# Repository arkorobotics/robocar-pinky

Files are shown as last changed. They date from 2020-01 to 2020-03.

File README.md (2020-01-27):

# Robocar - Pinky	

## Intro
Pinky is a 1/16 scale DIY autonomous car designed to compete in the [DIY Robocar](https://diyrobocars.com) race. Pinky also has a counterpart testbed named [Brain](Brain).

## Design

### Block Diagram
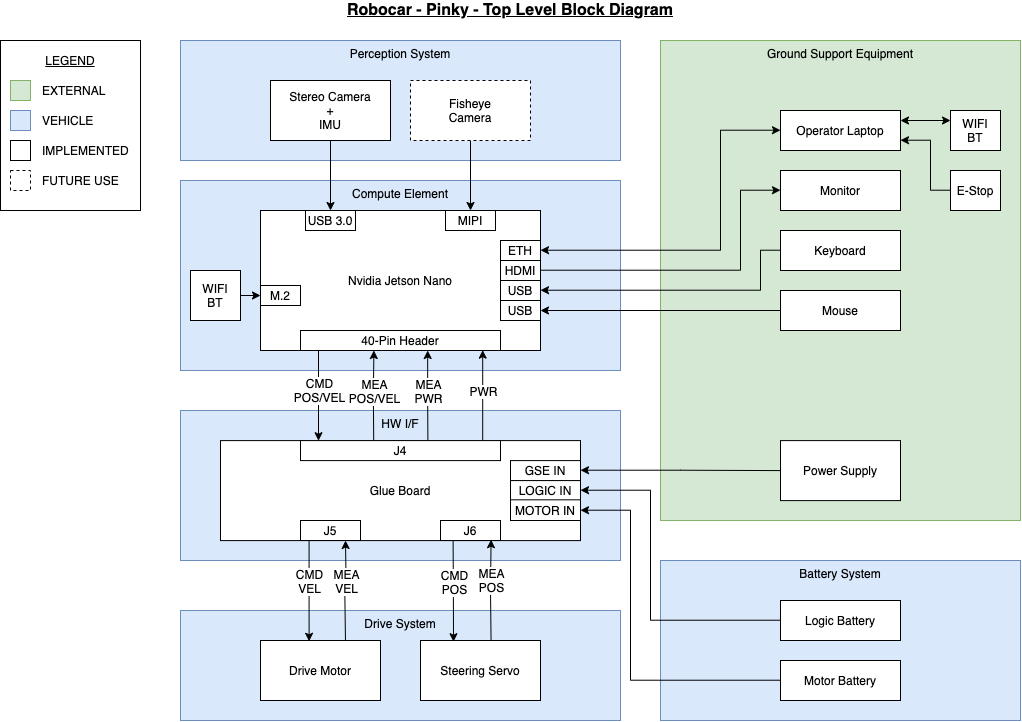
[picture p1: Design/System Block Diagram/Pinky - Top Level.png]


### Assembled Hardware
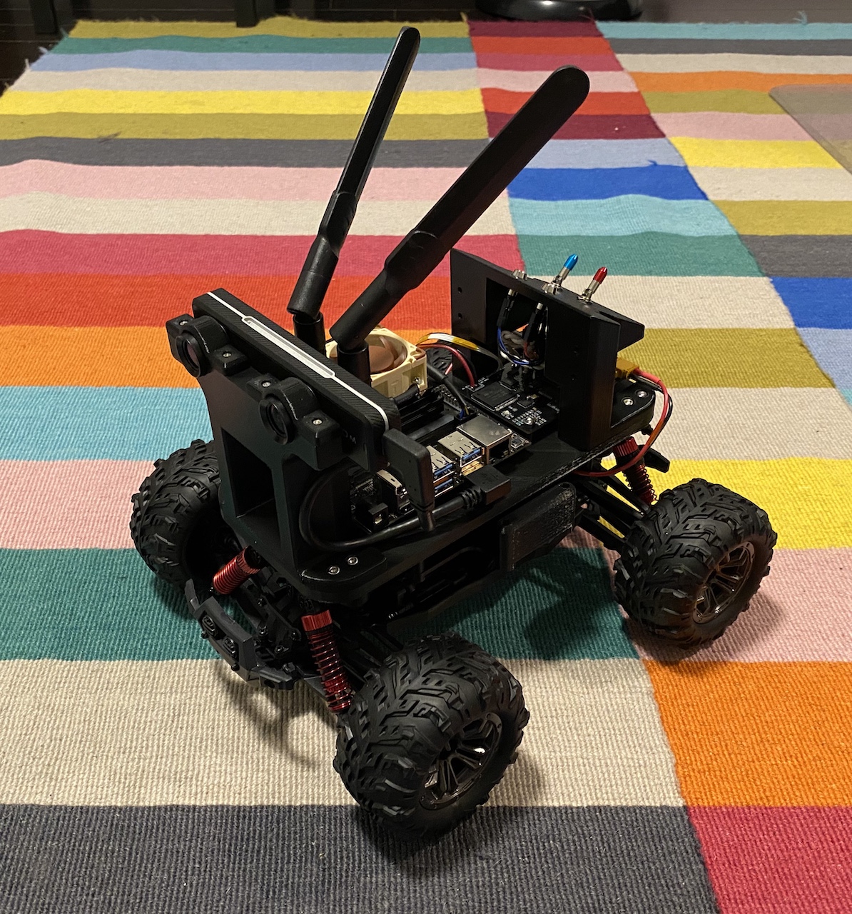
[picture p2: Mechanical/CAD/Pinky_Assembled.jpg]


## Software

See the [Software](./Software) subfolder.

## Hardware

### Perception System
Part | Cost  |  Link
------------ | ------------- | -------------
ZED Mini | $399.00 | [Stereo Labs Store](https://store.stereolabs.com/products/zed-mini)
IMX219 Camera Module (Fisheye) | $29.99  | [Amazon](https://www.amazon.com/gp/product/B07VFFRX4C)

### Compute Element
Part | Cost  |  Link
------------ | ------------- | -------------
NVIDIA Jetson Nano Developer Kit | $98.98 | [Amazon](https://www.amazon.com/gp/product/B07PZHBDKT/)
Intel Dual Band Wireless-Ac 8265 w/ BT Module | $21.55 | [Amazon](https://www.amazon.com/Intel-Dual-Band-Wireless-Ac-8265/dp/B01MZA1AB2)
Noctua Fan | $14.95 | [Amazon](https://www.amazon.com/gp/product/B071FNHVXN)

### Hardware Interface Board
Part | Cost  |  Link
------------ | ------------- | -------------
Glue Board (Fab/Assembly Required) | ~$300.00 | [GitHub](./Electronics/Glue%20Board)

### Drive System
Part | Cost  |  Link
------------ | ------------- | -------------
VATOS RC Car 9137R | $54.99 | [Amazon](https://www.amazon.com/gp/product/B07QRRJZDG/)

### Chassis
Part | Cost | Link
------------ | ------------- | -------------
Screw Set | $20.98 | [Amazon](https://www.amazon.com/gp/product/B07QLWPJKC/)
Threaded Heat Insert | $19.99 | [Amazon](https://www.amazon.com/gp/product/B07MWBJB67)
3D Printable Models (Fab/Assembly Required) | ~$20.00 | [GitHub](./Mechanical/CAD/STL%20Files)

### Other
Part | Cost  |  Link
------------ | ------------- | -------------
ENGPOW 7.4V 3000mah 30C Lipo Battery | $22.99 | [Amazon](https://www.amazon.com/gp/product/B075QDPSDQ/)
Samsung SD Car 128GB | $16.99 | [Amazon](https://www.amazon.com/gp/product/B06XWZWYVP/)
1.5 ft/50cm Micro USB 3.0 Cable | $8.79 | [Amazon](https://www.amazon.com/gp/product/B075CL915V/)
5V/4A 20W Switching Power | $8.99 | [Amazon](https://www.amazon.com/gp/product/B01N4HYWAM/)
WiFi/BT Antennas | $13.99 | [Amazon](https://www.amazon.com/gp/product/B01E29566W/)
USB 3.1 Right Angle A to Right Angle C | $19.25 | [UsbFirewire](https://www.usbfirewire.com/parts/rr-arch-xxg.html#RR-ARCH-10GRC)

### Harnessing
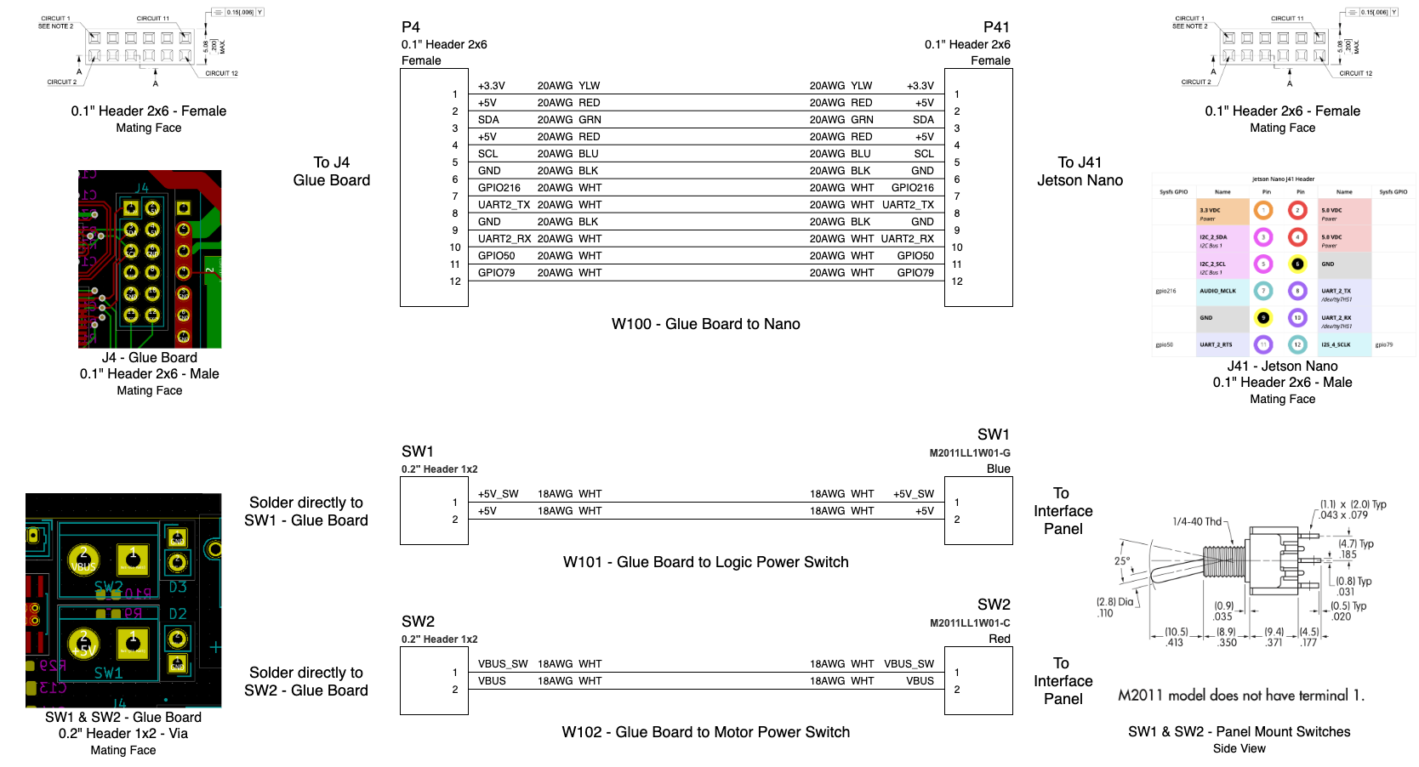
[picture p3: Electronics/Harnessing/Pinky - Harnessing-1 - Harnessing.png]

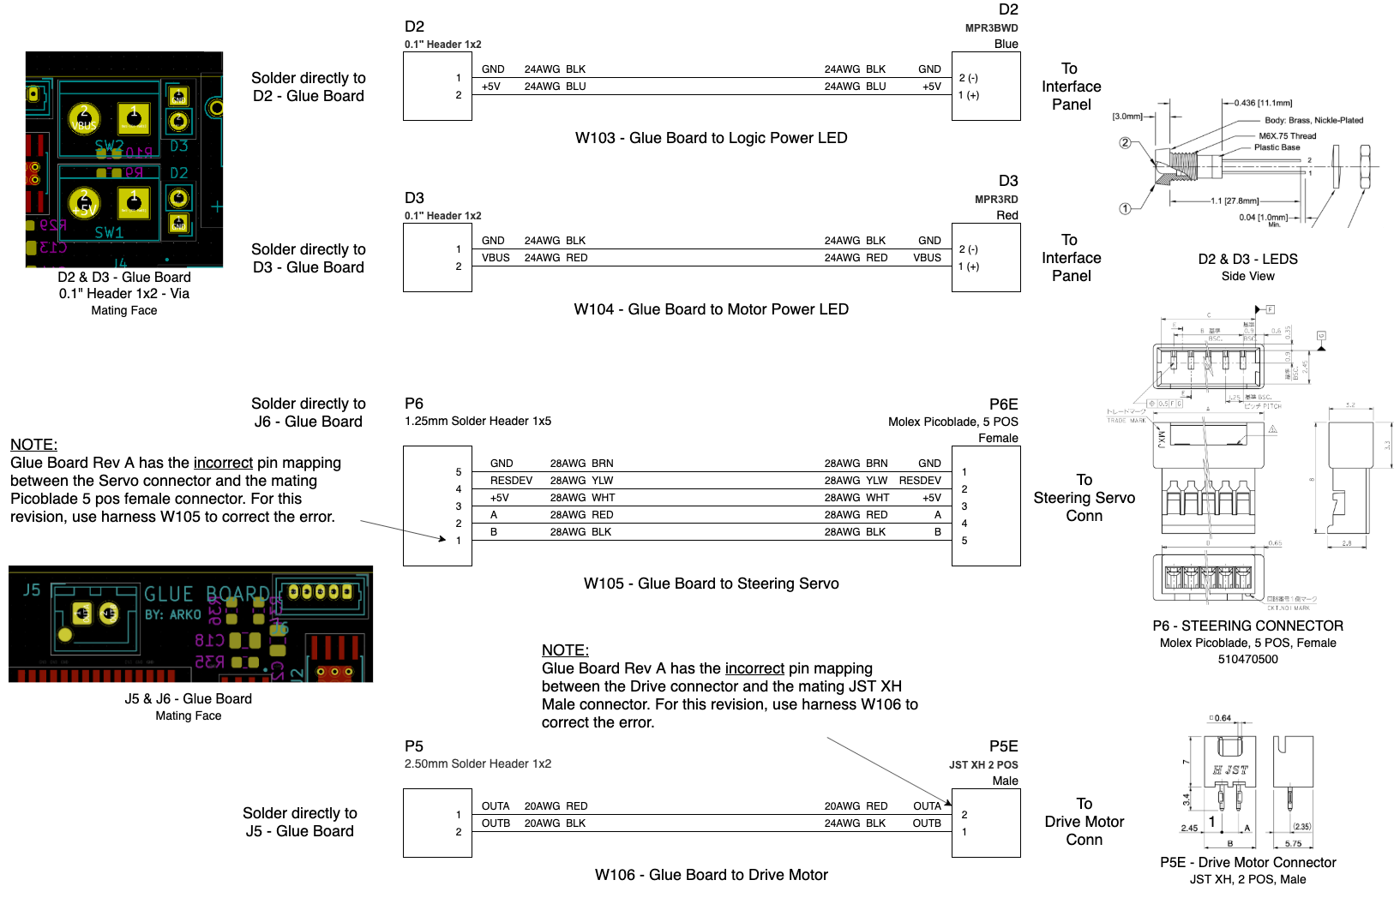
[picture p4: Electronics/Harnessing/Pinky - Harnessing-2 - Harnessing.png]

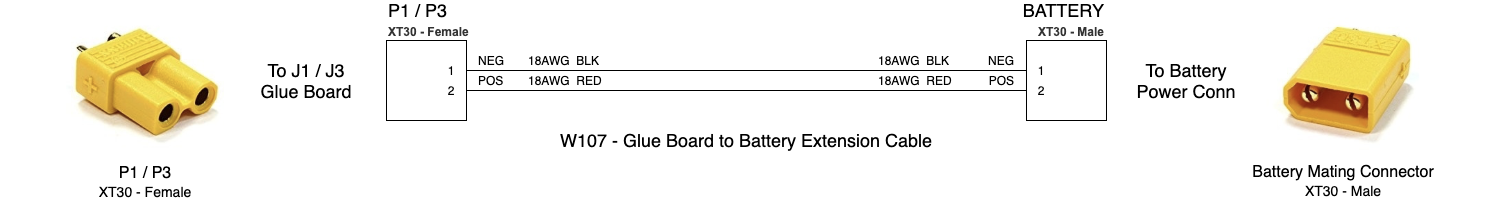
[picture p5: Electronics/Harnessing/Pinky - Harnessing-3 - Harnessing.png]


## Assembly

For 3D printed models, use the [Autodesk Fusion 360 Pinky CAD](./Mechanical/CAD/Pinky%20Assembly%20v27.f3z) model for assembly.

For electrical assembly, see diagram below:

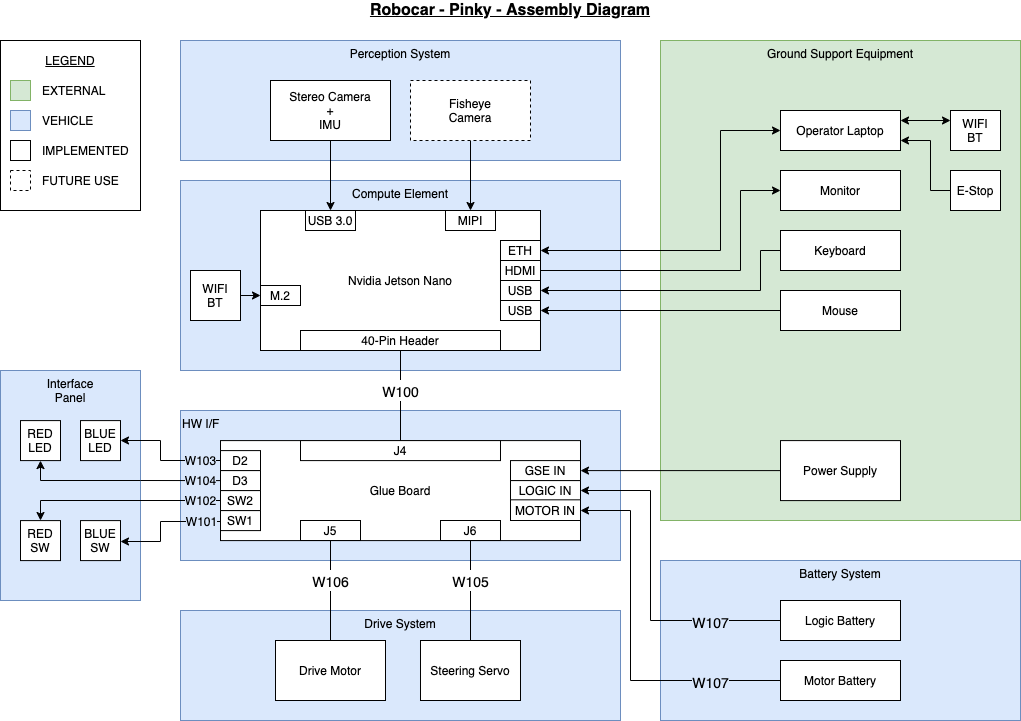
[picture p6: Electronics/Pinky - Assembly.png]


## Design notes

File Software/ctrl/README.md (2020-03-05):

Pinky Control Software
=======

## Configure Jetson I2C Bus
```
Update the I2C-A device clock rate by changing '/sys/bus/i2c/devices/i2c-1/bus_clk_rate' from 100000 to 400000
```

## Build
```
$ cd robocar-pinky/Software/ctrl
$ make
```

## Run
```
$ cd robocar-pinky/Software/ctrl
$ ./ctrl.sh
```

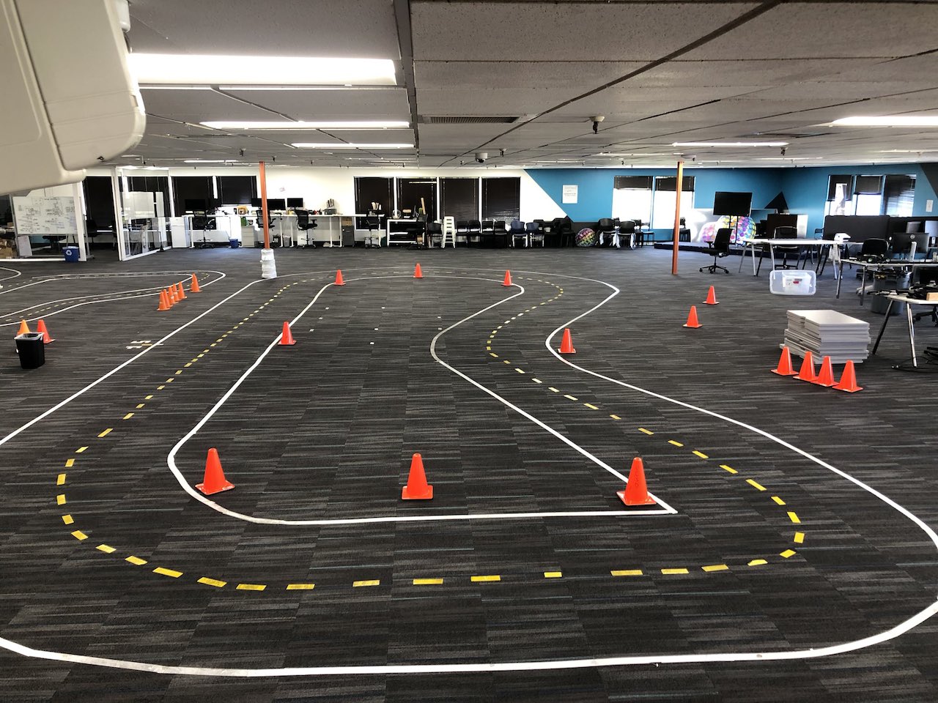
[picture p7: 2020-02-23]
Software/tb/track_above.jpg

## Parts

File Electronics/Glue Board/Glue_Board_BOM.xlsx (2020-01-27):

Reference | Quantity | Value | Footprint | Datasheet | MPN
C11 C18 C21 | 3 | 33nF | Capacitor_SMD:C_0805_2012Metric | ~ | C0805C333K5RACTU
C13 | 1 | 22uF | Capacitor_SMD:C_1210_3225Metric | ~ | C1210C226K3PACTU
C15 | 1 | 47uF | Capacitor_SMD:C_1210_3225Metric | ~ | GRM32EC81C476KE15L
C16 C12 C14 C10 | 4 | 0.1uF | Capacitor_SMD:C_0805_2012Metric | ~ | C0805C104Z5VACTU
C4 C1 C2 C7 C6 C17 C23 C22 | 8 | 1uF | Capacitor_SMD:C_0805_2012Metric | ~ | C0805C105K4RACTU
C5 C3 C9 | 3 | 100uF | Capacitor_SMD:C_1210_3225Metric | ~ | C1210C107M4PAC7800
C8 C20 C19 | 3 | 10uF | Capacitor_SMD:C_0805_2012Metric | ~ | C0805C106K4PACTU
D1 | 1 | STPS5L60S | agg:DO-214AB-SMC | ~ | STPS5L60S
D2 | 1 | LED | Connector_PinHeader_2.54mm:PinHeader_1x02_P2.54mm_Vertical | ~ | MPR3BWD
D3 | 1 | LED | Connector_PinHeader_2.54mm:PinHeader_1x02_P2.54mm_Vertical | ~ | MPR3RD
D4 | 1 | LED_Dual_2pin | LED_SMD:LED_1206_3216Metric | ~ | LTST-C235KGKRKT
J1 J3 | 2 | Conn_01x02_Male | Connector_AMASS:AMASS_XT30PW-M_1x02_P2.50mm_Horizontal | ~ | XT30PW-M
J2 | 1 | Barrel_Jack | Connector_BarrelJack:BarrelJack_Horizontal | ~ | PJ-102B
J4 | 1 | Conn_02x06_Odd_Even | Connector_PinHeader_2.54mm:PinHeader_2x06_P2.54mm_Vertical | ~ | 67997-112HLF
J5 | 1 | Conn_01x02_Male | Connector_JST:JST_XH_B2B-XH-AM_1x02_P2.50mm_Vertical | ~ | B2B-XH-A(LF)(SN)
J6 | 1 | Conn_01x05_Female | Connector_Molex:Molex_PicoBlade_53047-0510_1x05_P1.25mm_Vertical | ~ | 530470510
J7 | 1 | Conn_01x04_Male | Connector_PinHeader_2.54mm:PinHeader_1x04_P2.54mm_Vertical | ~
J8 | 1 | Conn_02x03_Odd_Even | Connector_IDC:IDC-Header_2x03_P2.54mm_Vertical | ~ | SFH11-NBPC-D03-ST-BK
JLBAT1 JVBUS1 JMBAT1 | 3 | TestPoint | TestPoint:TestPoint_Pad_D4.0mm | ~
PS1 | 1 | R-745.0D | libs:CONV_R-745.0D | Manufacturer Recommendations | R-745.0D
Q1 | 1 | CSD17501Q5A | Package_TO_SOT_SMD:TDSON-8-1 | http://www.ti.com/lit/gpn/csd17501q5a | CSD17501Q5A
R1 R6 | 2 | 23.7k | Resistor_SMD:R_0603_1608Metric | ~ | RC0603FR-0723K7L
R10 | 1 | 470 | Resistor_SMD:R_0603_1608Metric | ~ | ESR03EZPJ471
R19 R26 R11 R13 R12 R31 R32 R33 R34 R36 R39 R37 R40 R38 | 14 | 10k | Resistor_SMD:R_0603_1608Metric | ~ | RC0603FR-0710KL
R2 R7 R5 | 3 | 5k | Resistor_SMD:R_0603_1608Metric | ~ | CR0603-FX-4991ELF
R25 R27 R30 | 3 | 4.7k | Resistor_SMD:R_0603_1608Metric | ~ | ERJ-3EKF4751V
R28 R22 R21 R20 R23 R24 | 6 | 1k | Resistor_SMD:R_0603_1608Metric | ~ | RC0603JR-071KL
R29 | 1 | 30K | Resistor_SMD:R_0603_1608Metric | ~ | ERA-3AEB303V
R3 | 1 | 2.6k | Resistor_SMD:R_0603_1608Metric | ~ | RC0603FR-072K61L
R35 | 1 | 470R | Resistor_SMD:R_0603_1608Metric | ~ | ESR03EZPJ471
R4 | 1 | 10.2k | Resistor_SMD:R_0603_1608Metric | ~ | RC0603FR-0710K2L
R8 | 1 | 18.7k | Resistor_SMD:R_0603_1608Metric | ~ | RC0603FR-0718K7L
R9 | 1 | 47R | Resistor_SMD:R_0603_1608Metric | ~ | ESR03EZPJ470
SW1 | 1 | SW_SPST | TerminalBlock:TerminalBlock_bornier-2_P5.08mm | ~ | M2011LL1W01-G
SW2 | 1 | SW_SPST | TerminalBlock:TerminalBlock_bornier-2_P5.08mm | ~ | M2011LL1W01-C
TP1 | 1 | TestPoint | TestPoint:TestPoint_Pad_D2.0mm | ~
U1 | 1 | PCA9685PW | Package_SO:TSSOP-28_4.4x9.7mm_P0.65mm | http://www.nxp.com/documents/data_sheet/PCA9685.pdf | PCA9685PW/Q900,118
U2 | 1 | DRV8871DDA | Package_SO:Texas_HTSOP-8-1EP_3.9x4.9mm_P1.27mm_EP2.95x4.9mm_Mask2.4x3.1mm_ThermalVias | http://www.ti.com/lit/ds/symlink/drv8871.pdf | DRV8871DDAR
U3 | 1 | VNH5019ATR-E | Package_SO:ST_MultiPowerSO-30 | https://www.st.com/resource/en/datasheet/vnh5019a-e.pdf | VNH5019ATR-E
U4 | 1 | ADS1115IDGS | Package_SO:TSSOP-10_3x3mm_P0.5mm | http://www.ti.com/lit/ds/symlink/ads1113.pdf | ADS1115IDGSR
U5 | 1 | NCP1117-5.0_SOT223 | Package_TO_SOT_SMD:SOT-223-3_TabPin2 | http://www.onsemi.com/pub_link/Collateral/NCP1117-D.PDF | NCP1117LPST50T3G
U6 | 1 | TPS2121RUXR | libs:IC_TPS2121RUXR | TEXAS INSTRUMENTS | TPS2121RUXR
U7 | 1 | AMC1301DWVR | libs:SOIC127P1150X280-8N | TEXAS INSTRUMENTS | AMC1301DWVR
U8 U9 | 2 | INA260 | Package_SO:TSSOP-16_4.4x5mm_P0.65mm | http://www.ti.com/lit/ds/symlink/ina260.pdf | INA260AIPW

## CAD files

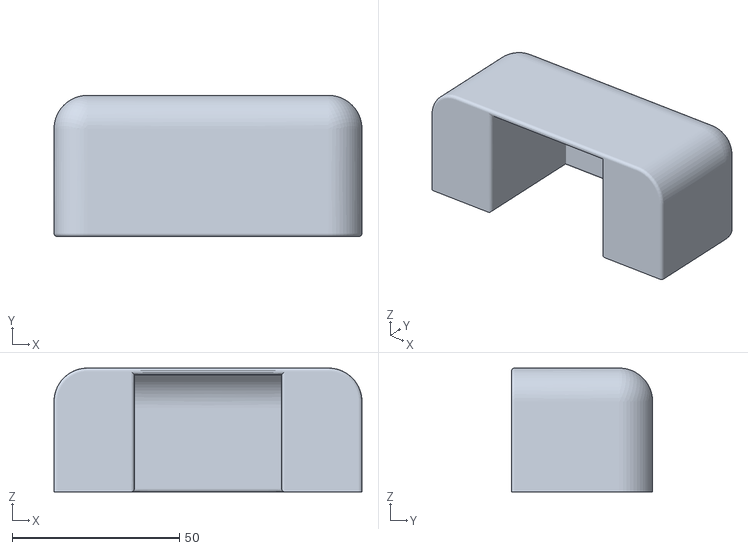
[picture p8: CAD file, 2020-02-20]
Mechanical/CAD/STL Files/Wire cover v6.stl
92.0 x 42.2 x 37.0

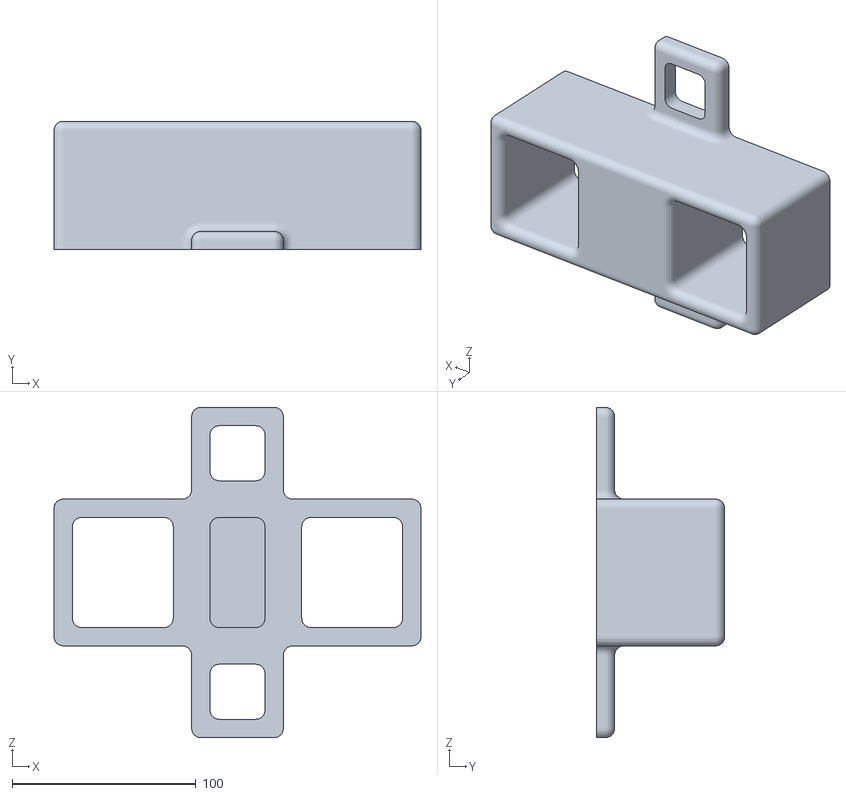
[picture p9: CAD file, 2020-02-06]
Mechanical/CAD/STL Files/Stand v2.stl
200.0 x 70.0 x 180.0

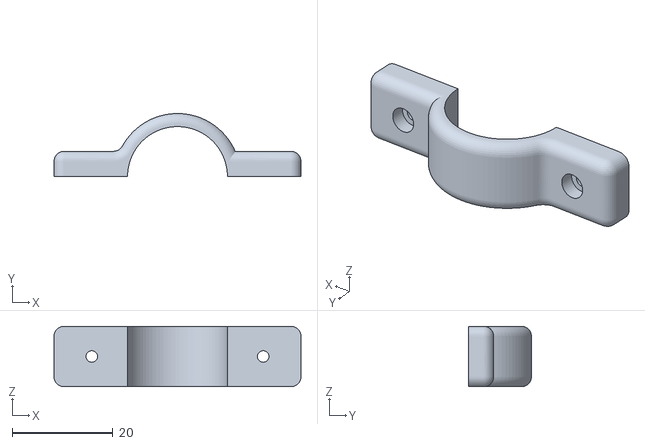
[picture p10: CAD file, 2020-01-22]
Mechanical/CAD/STL Files/Camera Lens Clamp v3.stl
49.0 x 12.5 x 12.0

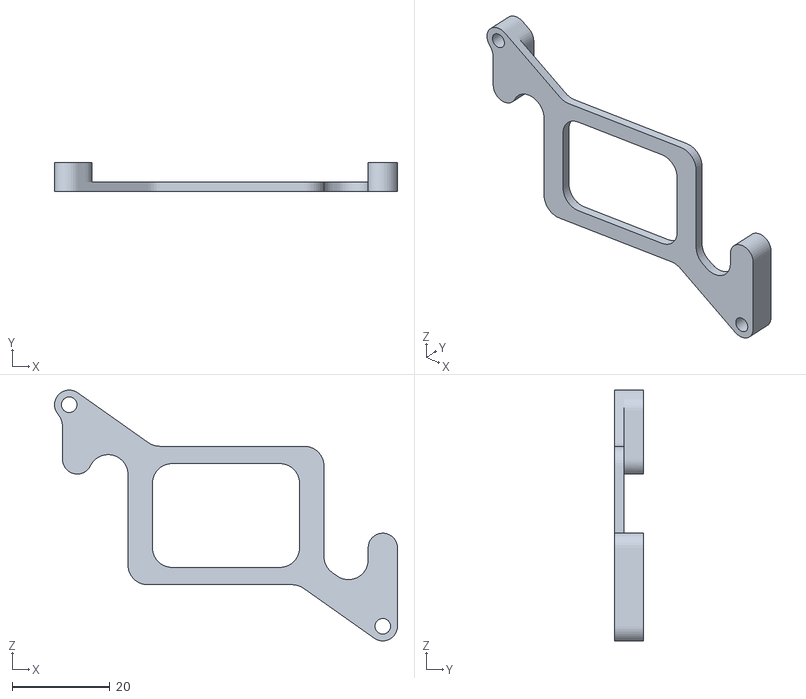
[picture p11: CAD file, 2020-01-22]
Mechanical/CAD/STL Files/Glue Board Spacer v8.stl
70.0 x 6.00 x 51.2

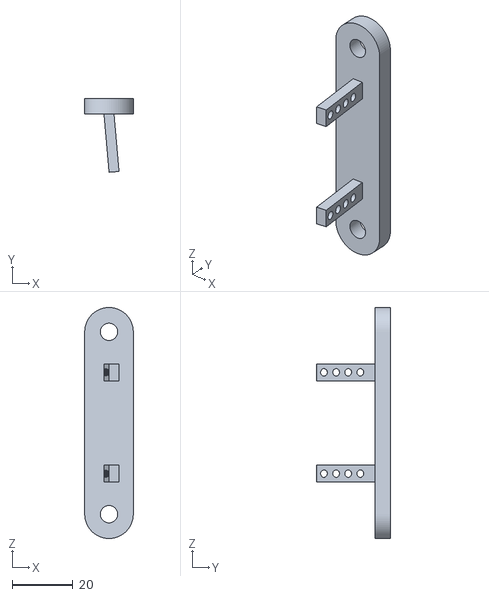
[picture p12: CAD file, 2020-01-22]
Mechanical/CAD/STL Files/Chassis - Aft Adapter v7.stl
16.0 x 24.2 x 76.0

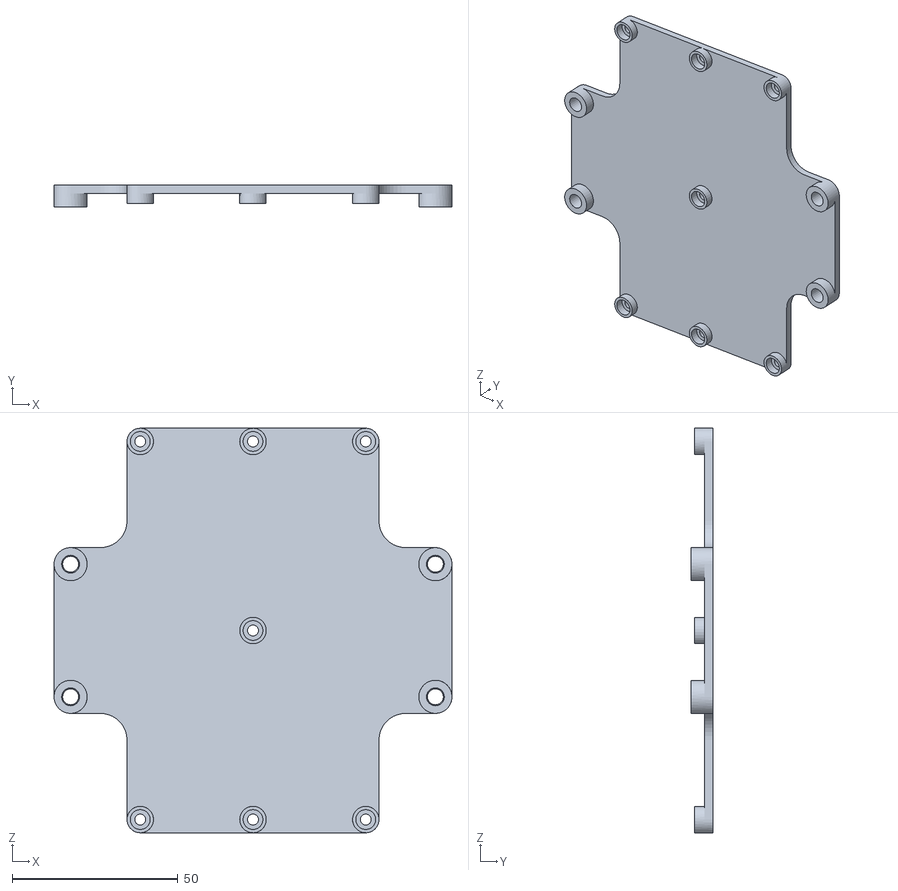
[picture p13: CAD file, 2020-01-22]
Mechanical/CAD/STL Files/Battery Bottom Plate v7.stl
120.0 x 6.54 x 122.0

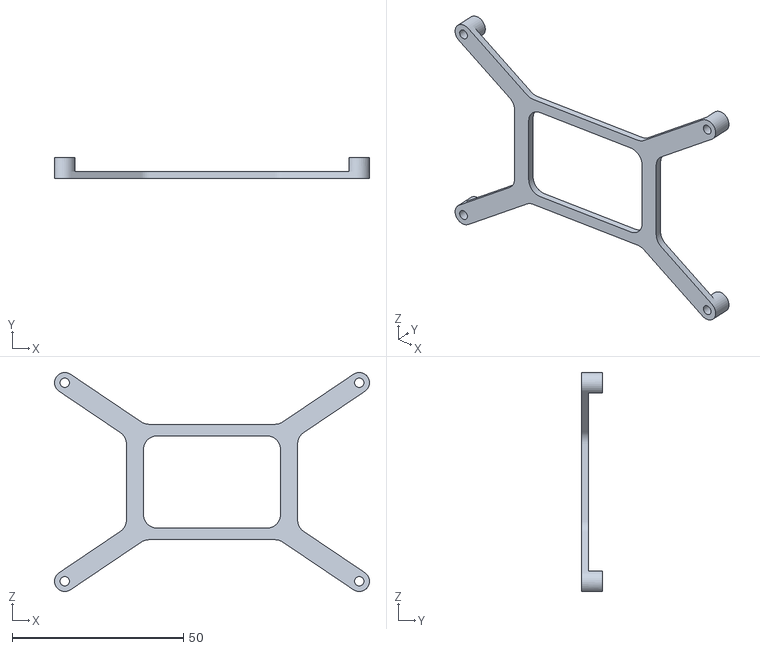
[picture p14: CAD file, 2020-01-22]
Mechanical/CAD/STL Files/Nano Spacer v2.stl
92.0 x 6.00 x 64.0

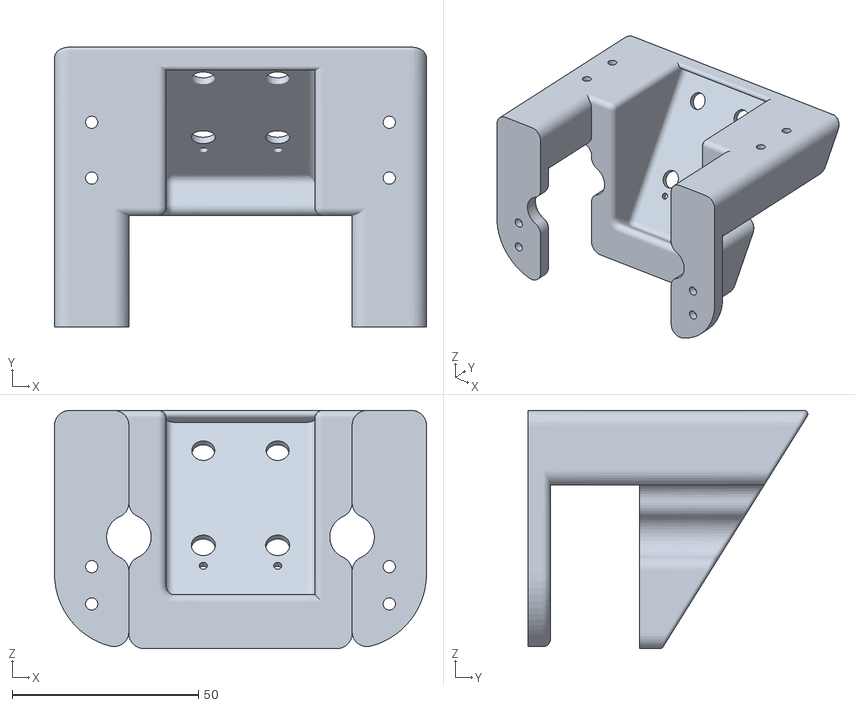
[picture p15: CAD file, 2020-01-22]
Mechanical/CAD/STL Files/Switch Mast v10.stl
100.0 x 75.2 x 64.0

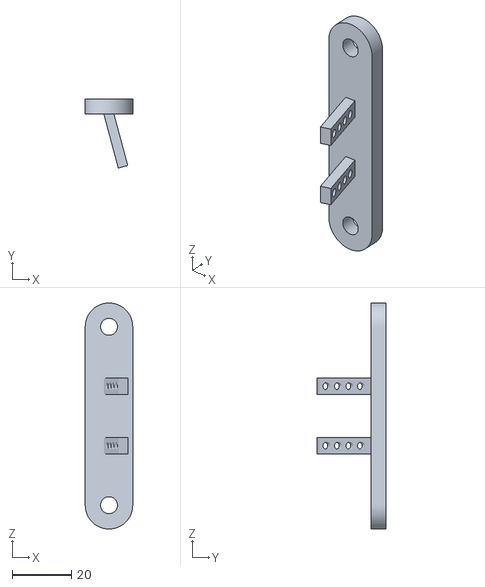
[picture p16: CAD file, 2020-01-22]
Mechanical/CAD/STL Files/Chassis - Front Adapter v5.stl
16.0 x 23.2 x 76.0

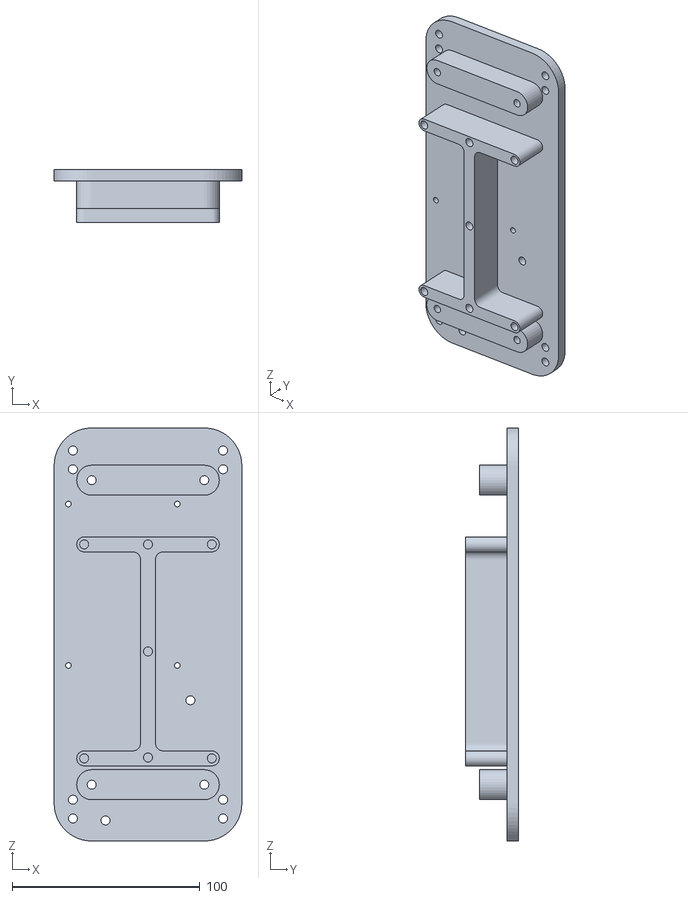
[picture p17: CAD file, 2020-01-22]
Mechanical/CAD/STL Files/Base Plate v27.stl
100.0 x 28.2 x 220.0

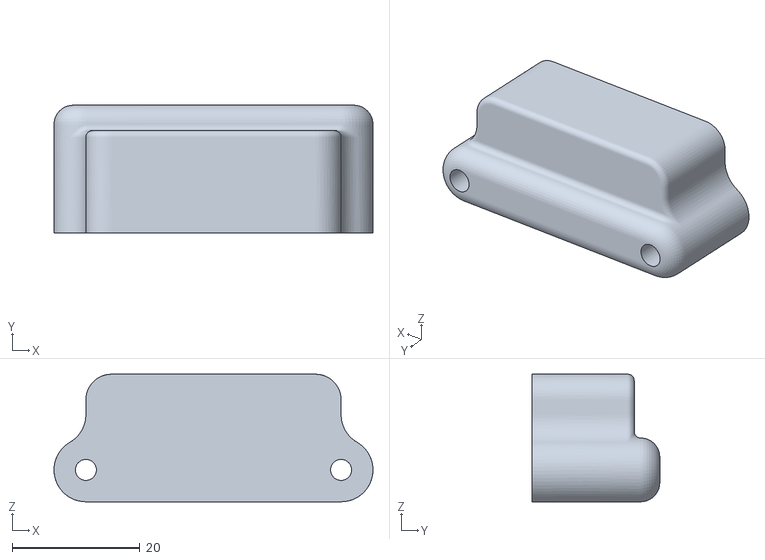
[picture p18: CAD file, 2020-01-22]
Mechanical/CAD/STL Files/Battery Side Wall v5.stl
50.0 x 20.0 x 20.0

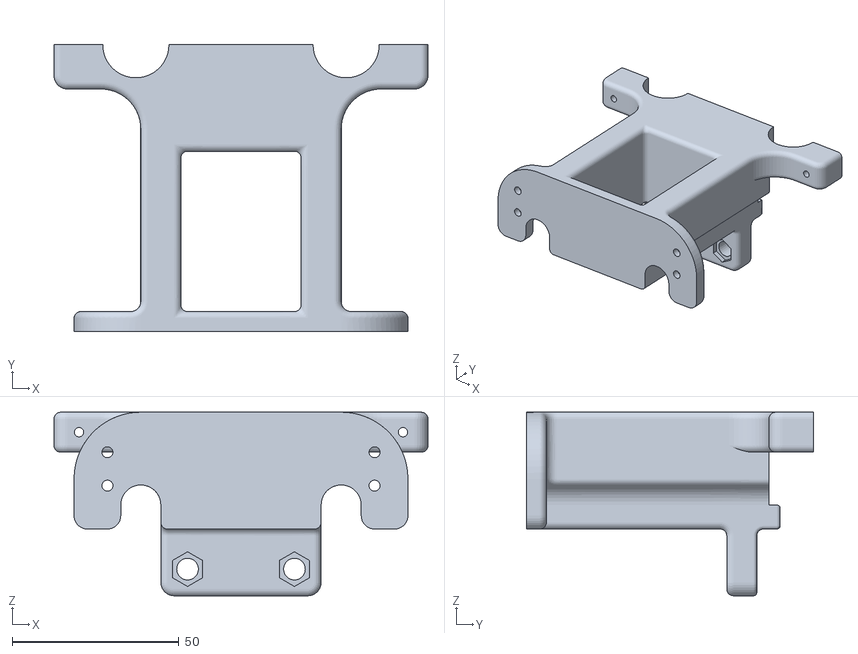
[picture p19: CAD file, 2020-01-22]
Mechanical/CAD/STL Files/Camera Mast v8.stl
112.0 x 86.0 x 55.0

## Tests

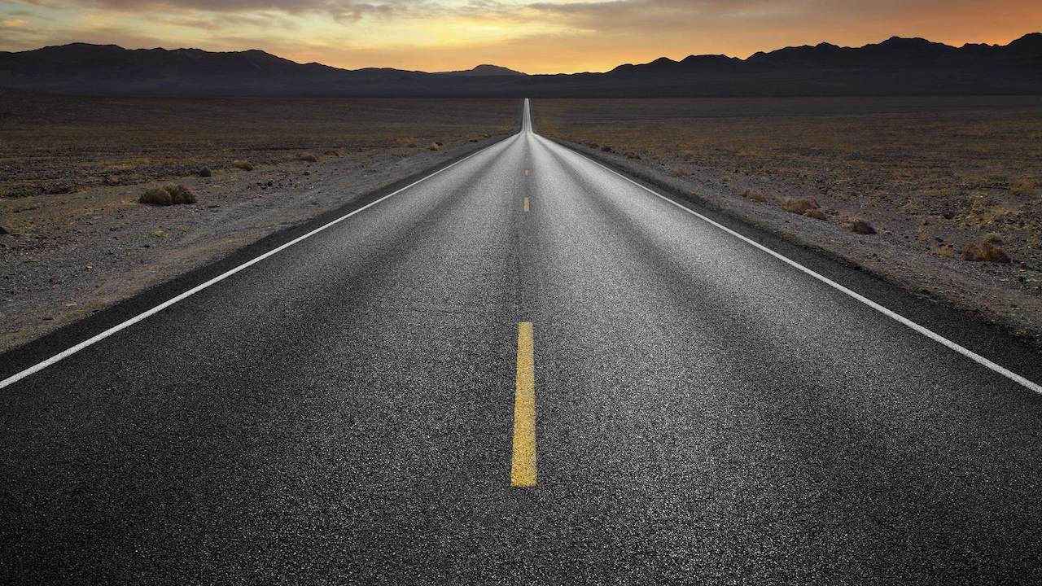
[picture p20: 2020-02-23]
Software/tb/test_road_image.jpg

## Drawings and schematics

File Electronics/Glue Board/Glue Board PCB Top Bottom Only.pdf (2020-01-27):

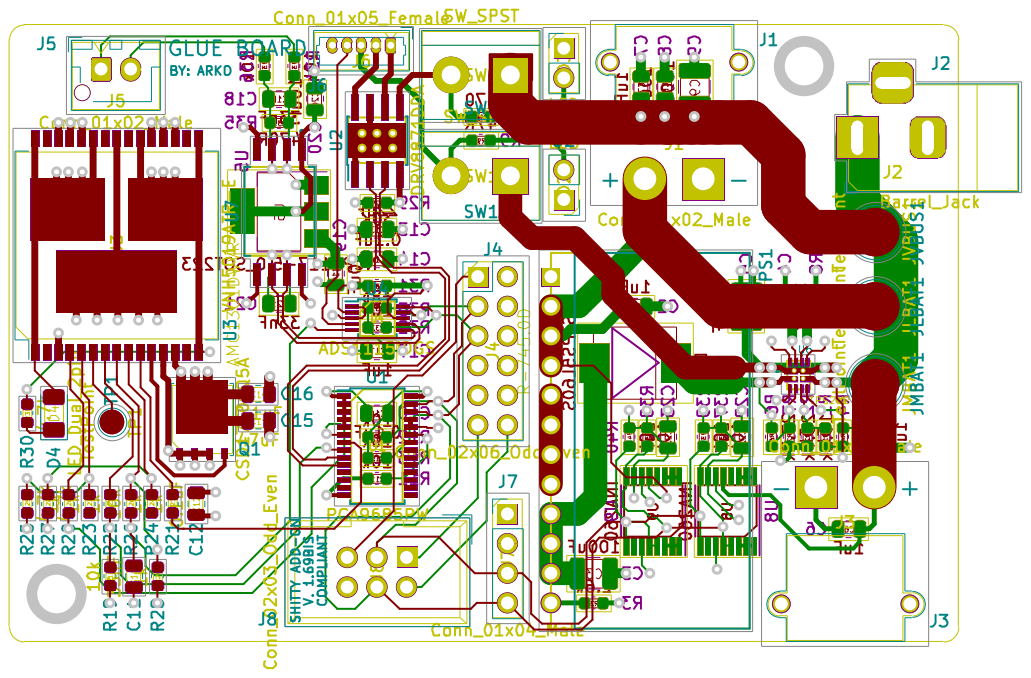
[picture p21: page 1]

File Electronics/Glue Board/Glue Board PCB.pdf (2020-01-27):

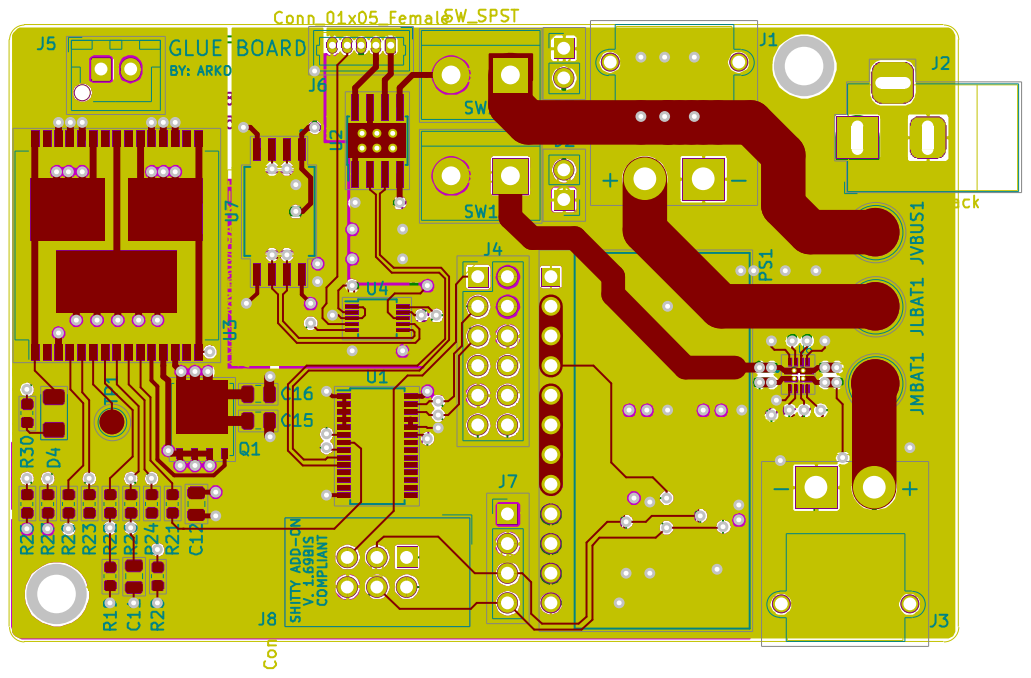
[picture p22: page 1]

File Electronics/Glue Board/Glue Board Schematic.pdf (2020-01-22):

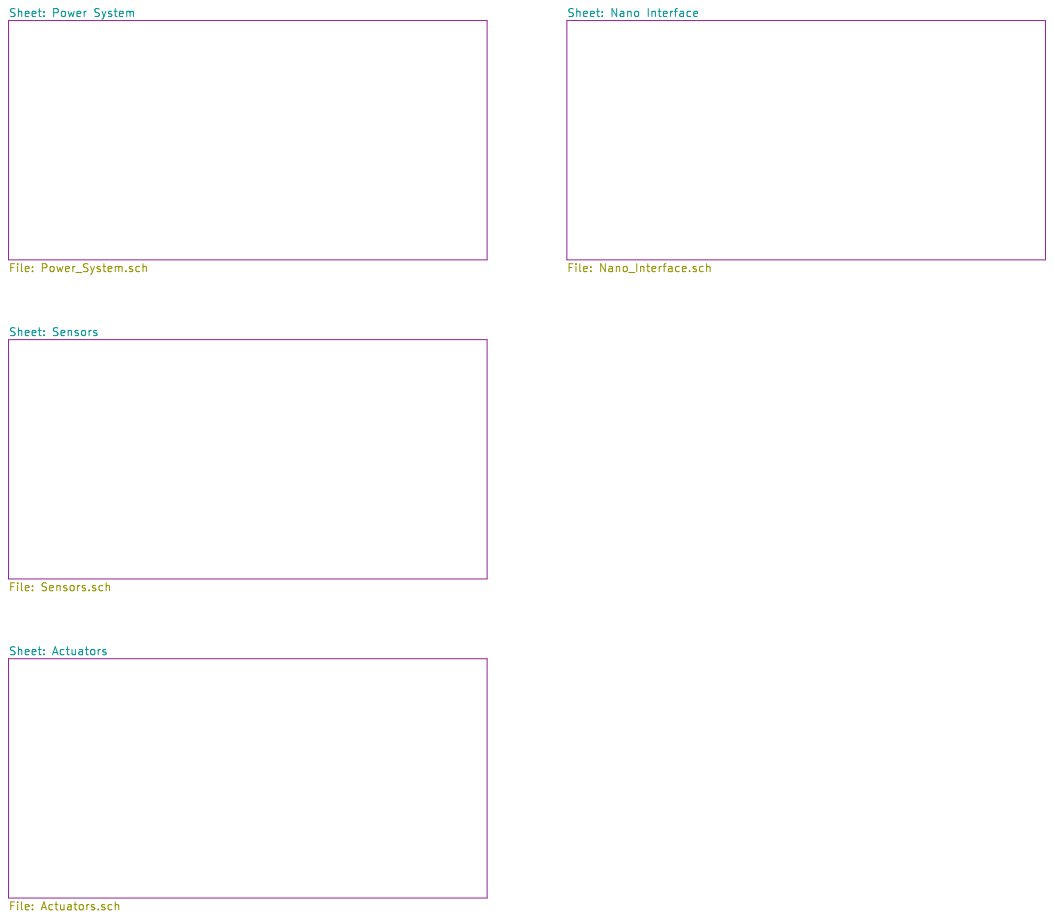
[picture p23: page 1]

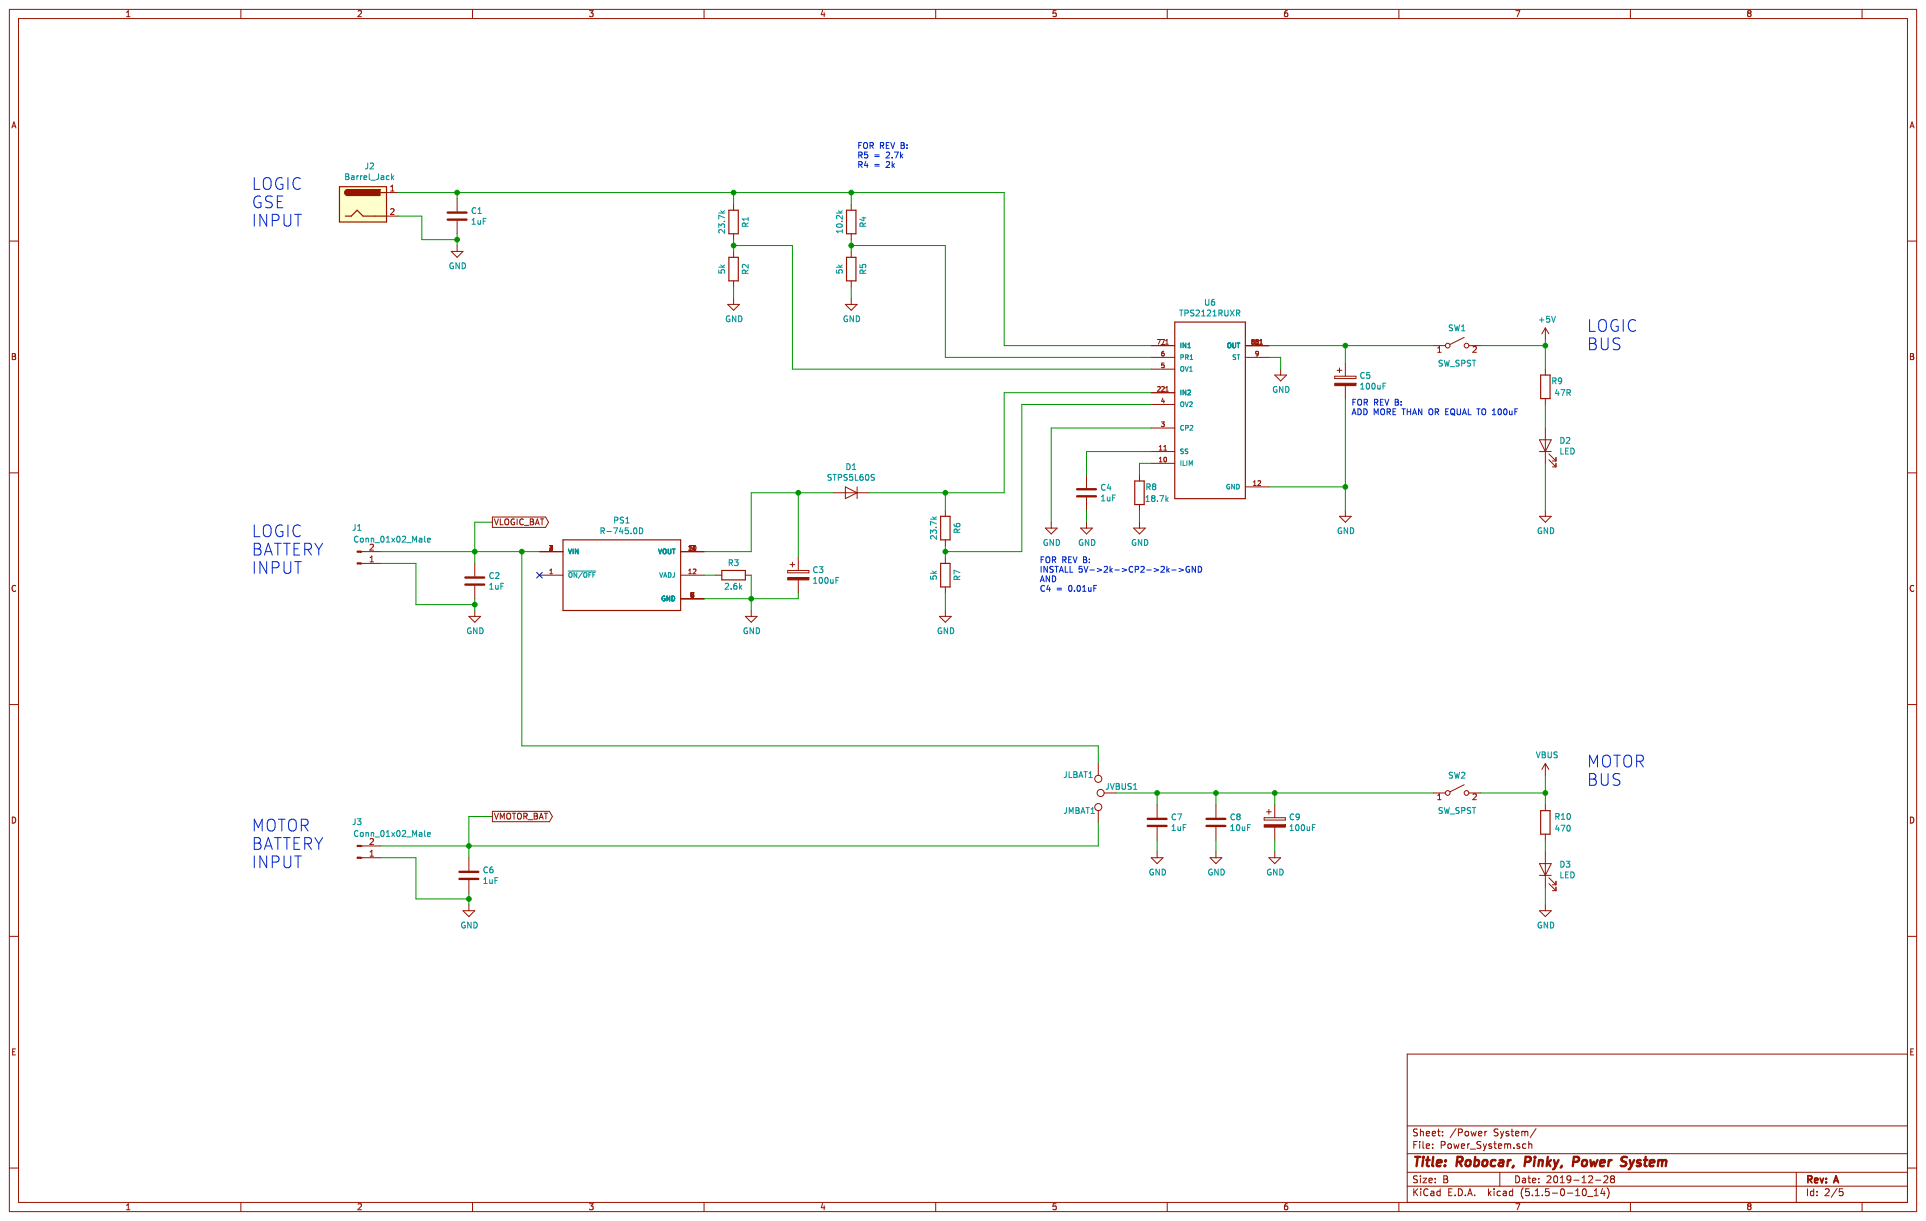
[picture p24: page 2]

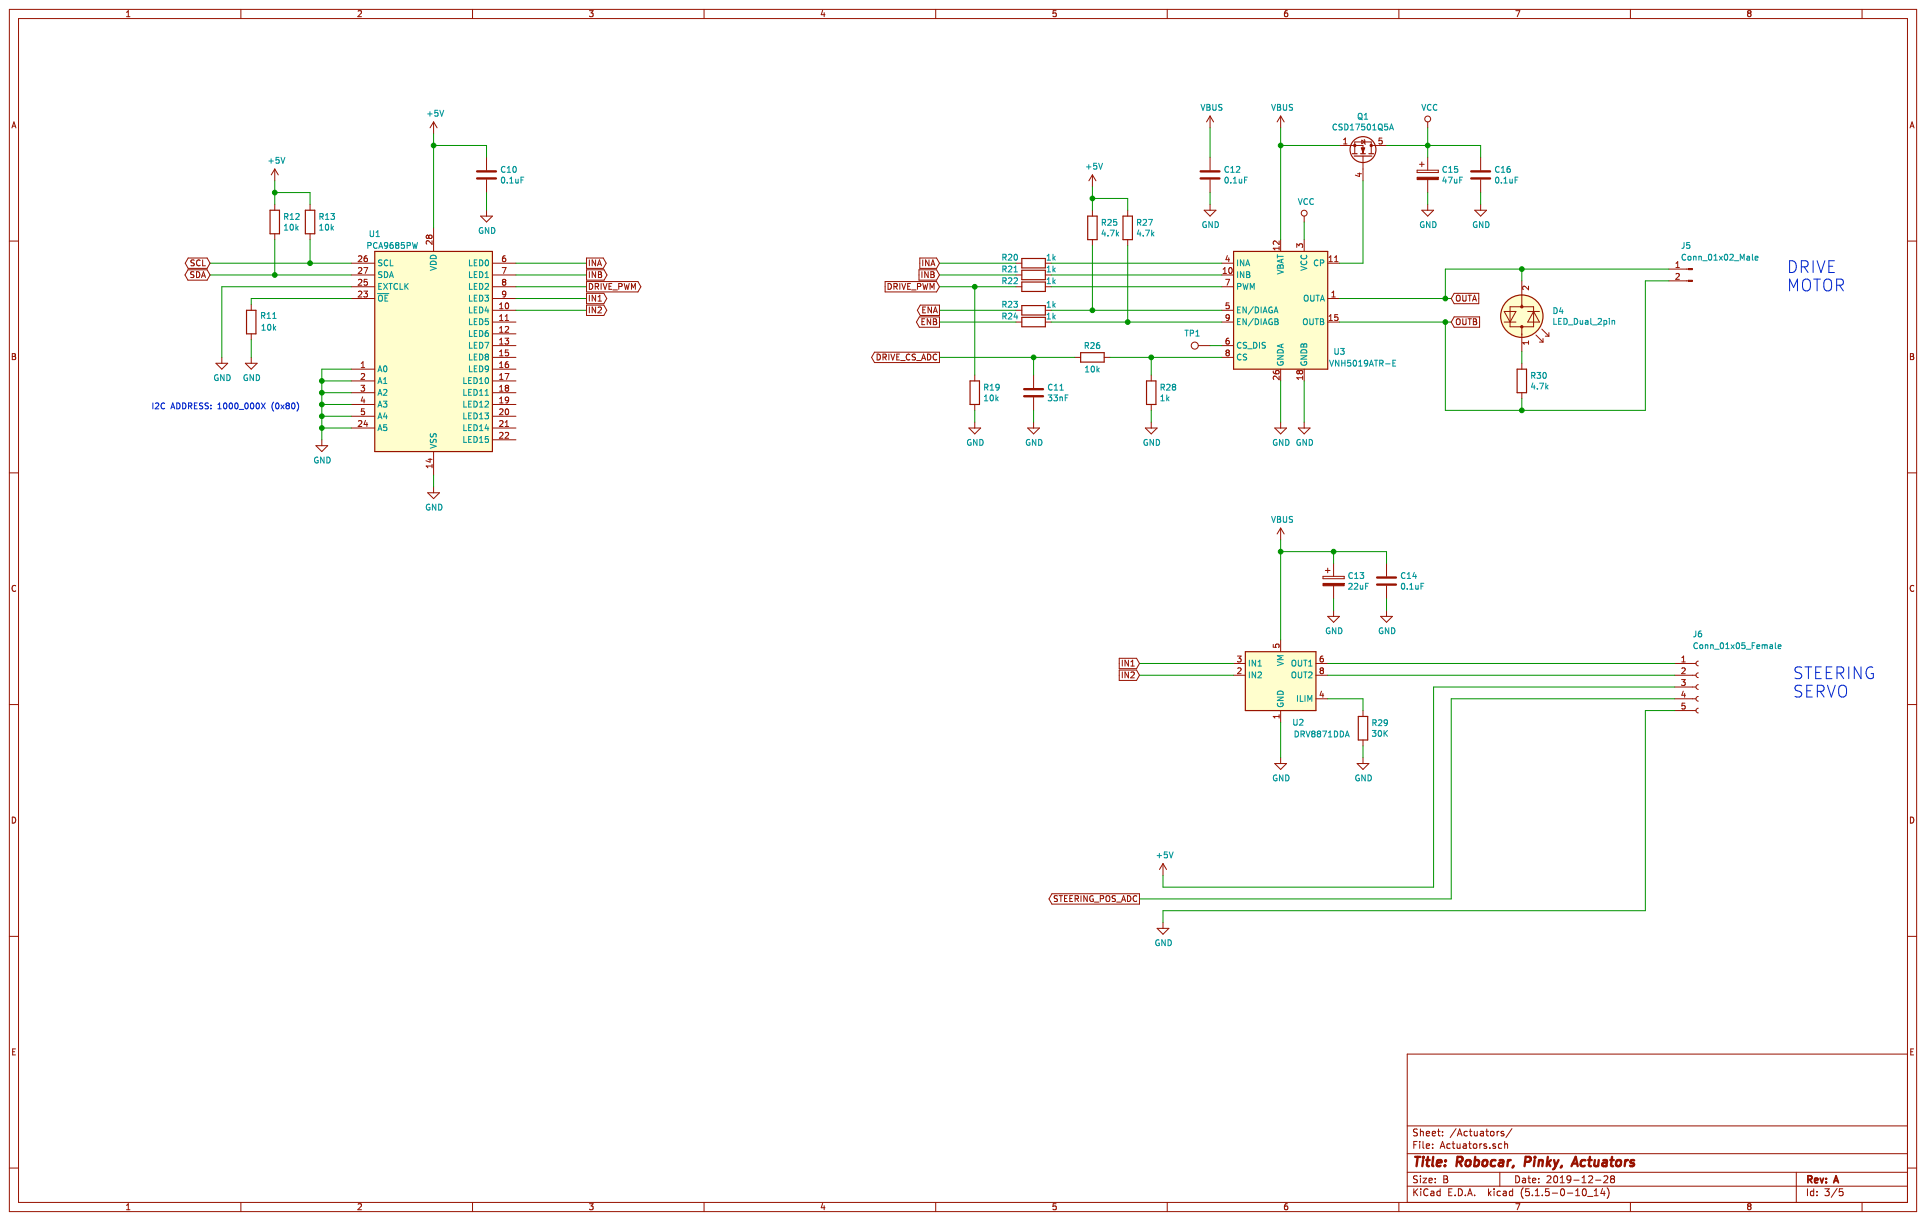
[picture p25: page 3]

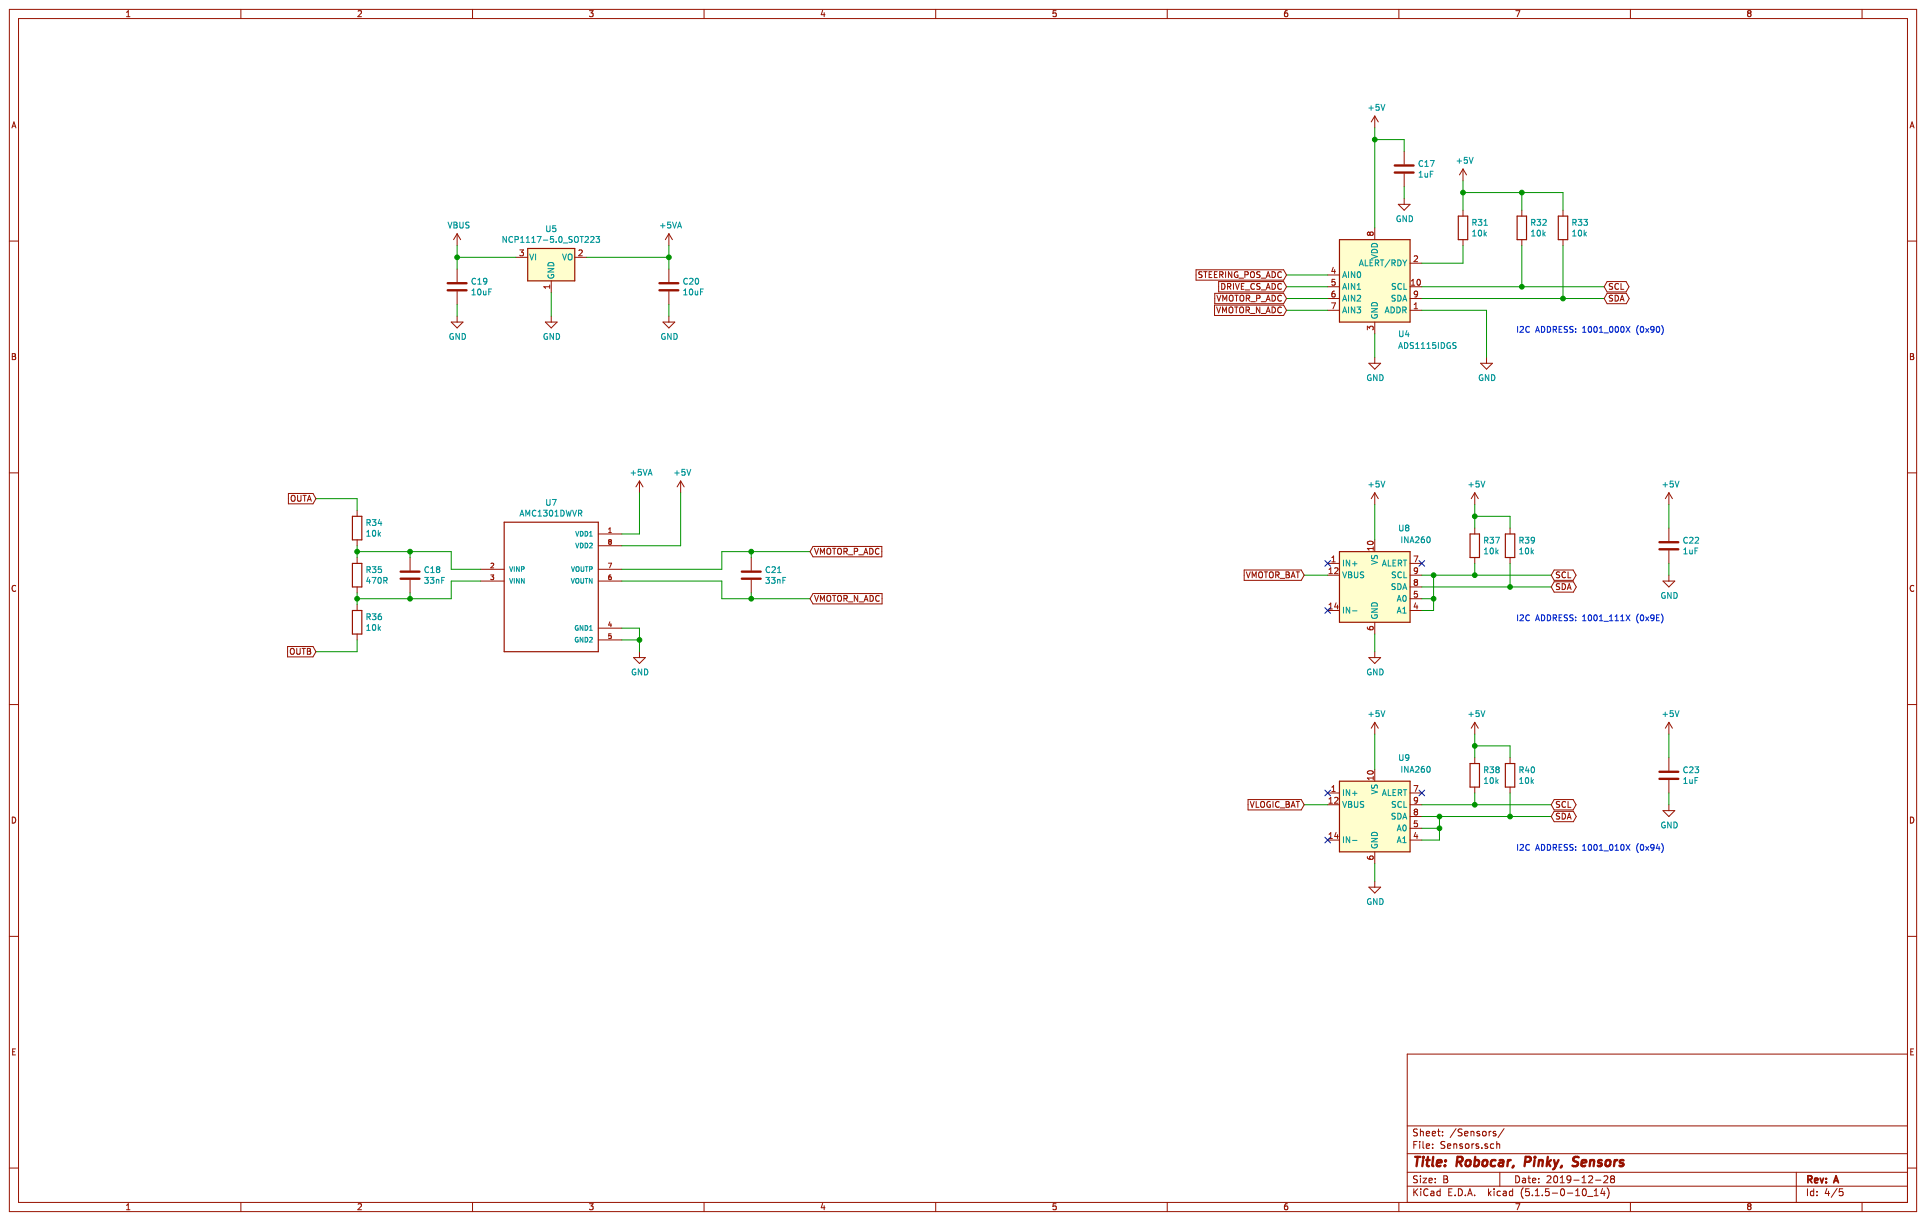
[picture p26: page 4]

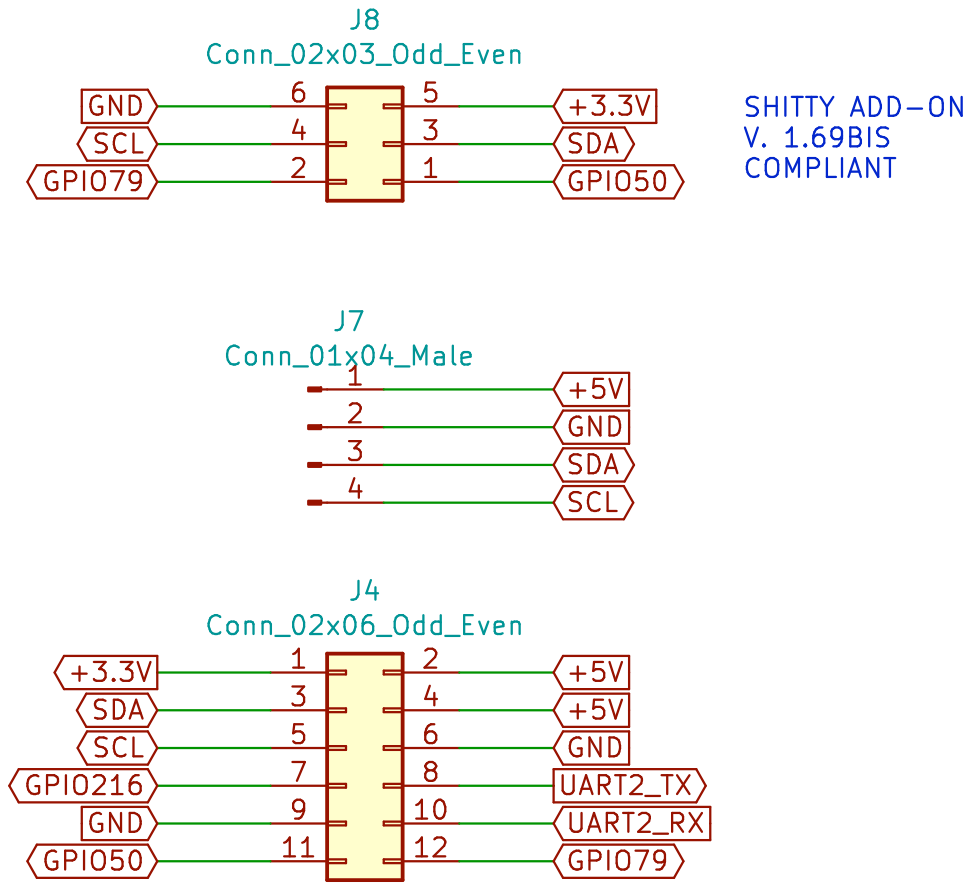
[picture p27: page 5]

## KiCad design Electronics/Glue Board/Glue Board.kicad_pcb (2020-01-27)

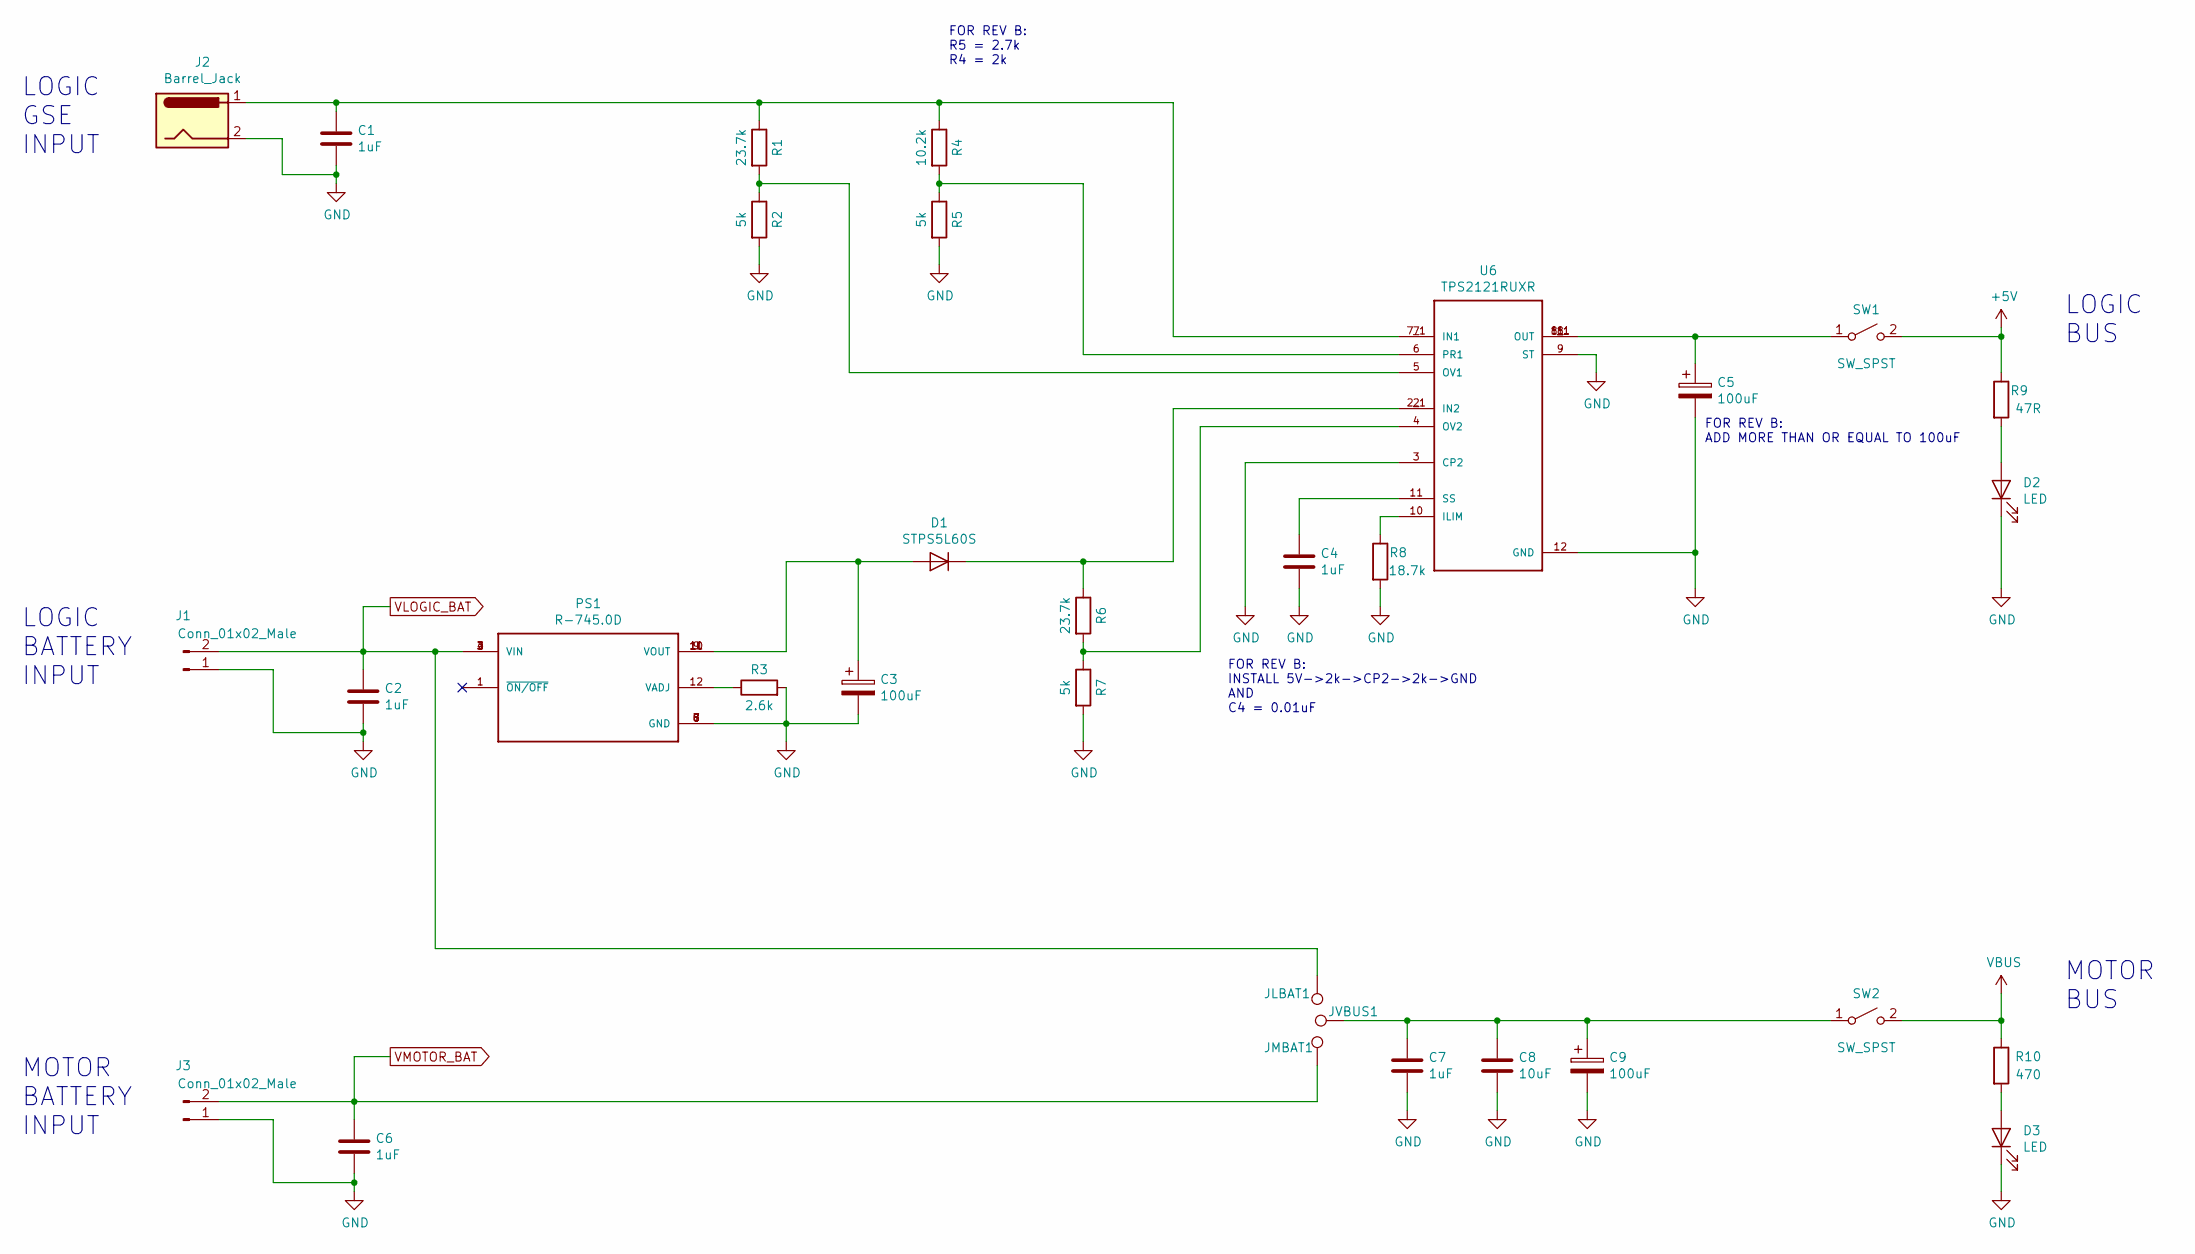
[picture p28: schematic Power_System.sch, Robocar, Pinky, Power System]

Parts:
C1, C2, C4, C6, C7: 1uF; C_0805_2012Metric; MPN C0805C105K4RACTU
C3, C5, C9: 100uF; C_1210_3225Metric; MPN C1210C107M4PAC7800
C8: 10uF; C_0805_2012Metric; MPN C0805C106K4PACTU
D1: STPS5L60S; DO-214AB-SMC; MPN STPS5L60S
D2, D3: LED; PinHeader_1x02_P2.54mm_Vertical; MPN MPR3BWD
J1, J3: Conn_01x02_Male; AMASS_XT30PW-M_1x02_P2.50mm_Horizontal; MPN XT30PW-M
J2: Barrel_Jack; BarrelJack_Horizontal; MPN PJ-102B
JLBAT1: TestPoint; TestPoint_Pad_D4.0mm
JMBAT1: TestPoint; TestPoint_Pad_D4.0mm
JVBUS1: TestPoint; TestPoint_Pad_D4.0mm
PS1: R-745.0D; CONV_R-745.0D; MPN R-745.0D
R1, R6: 23.7k; R_0603_1608Metric; MPN RC0603FR-0723K7L
R2, R5, R7: 5k; R_0603_1608Metric; MPN CR0603-FX-4991ELF
R3: 2.6k; R_0603_1608Metric; MPN RC0603FR-072K61L
R4: 10.2k; R_0603_1608Metric; MPN RC0603FR-0710K2L
R8: 18.7k; R_0603_1608Metric; MPN RC0603FR-0718K7L
R9: 47R; R_0603_1608Metric; MPN ESR03EZPJ470
R10: 470; R_0603_1608Metric; MPN ESR03EZPJ471
SW1: SW_SPST; TerminalBlock_bornier-2_P5.08mm; MPN M2011LL1W01-G
SW2: SW_SPST; TerminalBlock_bornier-2_P5.08mm; MPN M2011LL1W01-C
U6: TPS2121RUXR; IC_TPS2121RUXR; MPN TPS2121RUXR

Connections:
+5V: R9.1, SW1.2 (B); also elsewhere on the board
GND: C1.2, C2.2, C3.2, C4.2, C5.2, C6.2, C7.2, C8.2, C9.2, D2.1 (K), D3.1 (K), J1.1, J2.2, J3.1, PS1.5 (GND), PS1.6 (GND), PS1.7 (GND), PS1.8 (GND), R2.2, R3.2, R5.2, R7.2, R8.2, U6.3 (CP2), U6.9 (ST), U6.12 (GND); also elsewhere on the board
unnamed: C1.1, J2.1, R1.1, R4.1, U6.7 (IN1), U6.7_1 (IN1)
unnamed: C3.1, D1.2 (A), PS1.9 (VOUT), PS1.10 (VOUT), PS1.11 (VOUT)
unnamed: C4.1, U6.11 (SS)
unnamed: C5.1, SW1.1 (A), U6.1 (OUT), U6.1_1 (OUT), U6.8 (OUT), U6.8_1 (OUT)
unnamed: C7.1, C8.1, C9.1, JVBUS1.1, SW2.1 (A)
unnamed: D1.1 (K), R6.1, U6.2 (IN2), U6.2_1 (IN2)
unnamed: D2.2 (A), R9.2
unnamed: D3.2 (A), R10.2
unnamed: PS1.12 (VADJ), R3.1
unnamed: R1.2, R2.1, U6.5 (OV1)
unnamed: R4.2, R5.1, U6.6 (PR1)
unnamed: R6.2, R7.1, U6.4 (OV2)
unnamed: R8.1, U6.10 (ILIM)
VBUS: R10.1, SW2.2 (B); also elsewhere on the board
VLOGIC_BAT: C2.1, J1.2, JLBAT1.1, PS1.2 (VIN), PS1.3 (VIN), PS1.4 (VIN); also elsewhere on the board
VMOTOR_BAT: C6.1, J3.2, JMBAT1.1; also elsewhere on the board

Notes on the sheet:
LOGIC GSE INPUT
LOGIC BATTERY INPUT
MOTOR BUS
LOGIC BUS
MOTOR BATTERY INPUT
FOR REV B: INSTALL 5V->2k->CP2->2k->GND AND C4 = 0.01uF
FOR REV B: R5 = 2.7k R4 = 2k
FOR REV B: ADD MORE THAN OR EQUAL TO 100uF

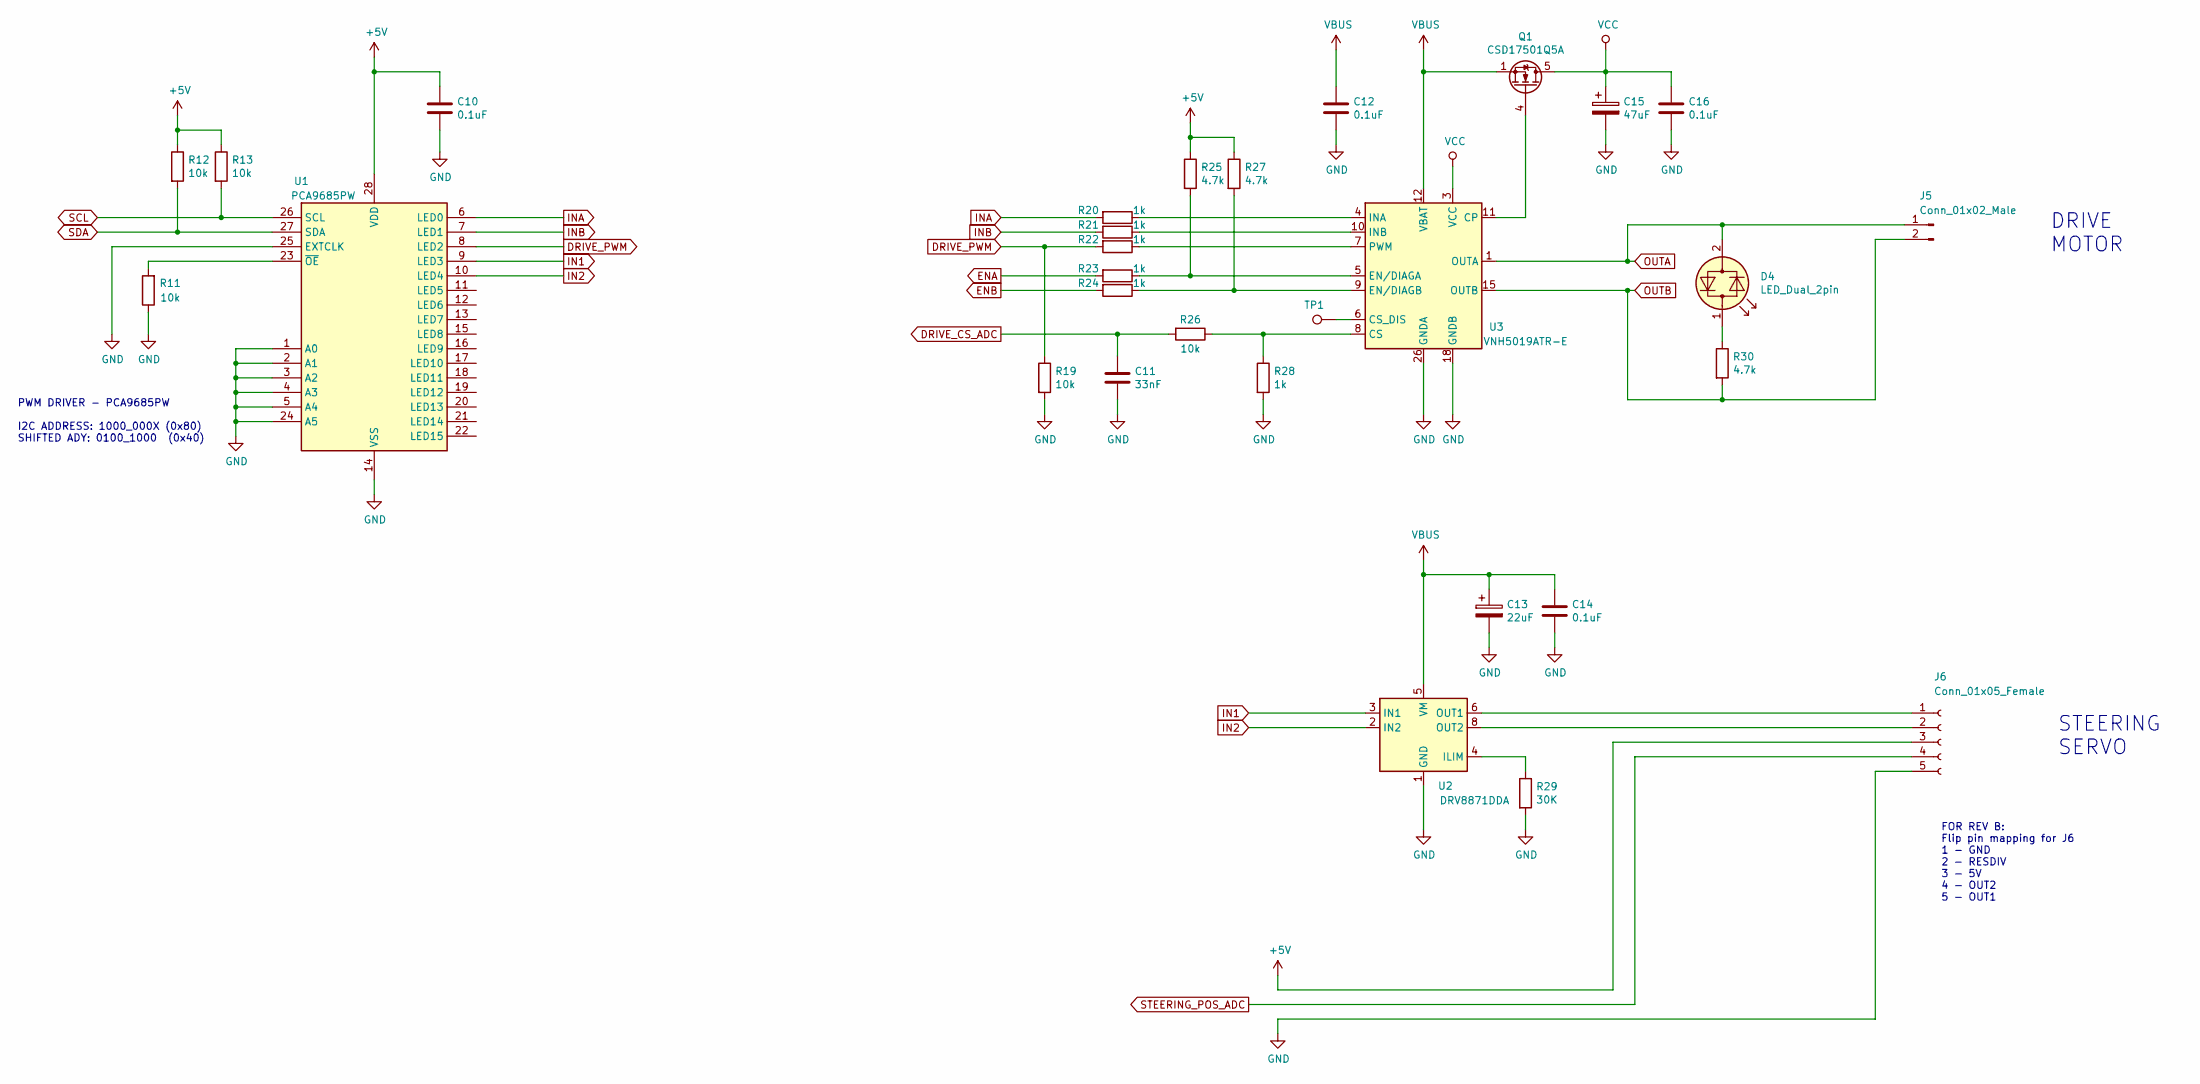
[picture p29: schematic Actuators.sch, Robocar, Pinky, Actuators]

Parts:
C10, C12, C14, C16: 0.1uF; C_0805_2012Metric; MPN C0805C104Z5VACTU
C11: 33nF; C_0805_2012Metric; MPN C0805C333K5RACTU
C13: 22uF; C_1210_3225Metric; MPN C1210C226K3PACTU
C15: 47uF; C_1210_3225Metric; MPN GRM32EC81C476KE15L
D4: LED_Dual_2pin; LED_1206_3216Metric; MPN LTST-C235KGKRKT
J5: Conn_01x02_Male; JST_XH_B2B-XH-AM_1x02_P2.50mm_Vertical; MPN B2B-XH-A(LF)(SN)
J6: Conn_01x05_Female; Molex_PicoBlade_53047-0510_1x05_P1.25mm_Vertical; MPN 0530470510
Q1: CSD17501Q5A; TDSON-8-1; MPN CSD17501Q5A
R11, R12, R13, R19, R26: 10k; R_0603_1608Metric; MPN RC0603FR-0710KL
R20, R21, R22, R23, R24, R28: 1k; R_0603_1608Metric; MPN RC0603JR-071KL
R25, R27, R30: 4.7k; R_0603_1608Metric; MPN ERJ-3EKF4751V
R29: 30K; R_0603_1608Metric; MPN ERA-3AEB303V
TP1: TestPoint; TestPoint_Pad_D2.0mm
U1: PCA9685PW; TSSOP-28_4.4x9.7mm_P0.65mm; MPN PCA9685PW
U2: DRV8871DDA; Texas_HTSOP-8-1EP_3.9x4.9mm_P1.27mm_EP2.95x4.9mm_Mask2.4x3.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; MPN DRV8871DDAR
U3: VNH5019ATR-E; ST_MultiPowerSO-30; MPN VNH5019ATR-E

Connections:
+5V: C10.1, J6.3, R12.1, R13.1, R25.1, R27.1, U1.28 (VDD); also elsewhere on the board
DRIVE_CS_ADC: C11.1, R26.2; also elsewhere on the board
DRIVE_PWM: R19.1, R22.2, U1.8 (LED2)
ENA: R23.2
ENB: R24.2
GND: C10.2, C11.2, C12.2, C13.2, C14.2, C15.2, C16.2, J6.5, R11.1, R19.2, R28.2, R29.2, U1.1 (A0), U1.2 (A1), U1.3 (A2), U1.4 (A3), U1.5 (A4), U1.14 (VSS), U1.24 (A5), U1.25 (EXTCLK), U2.1 (GND), U2.7 (GND), U2.9 (GND), U3.18 (GNDB), U3.19 (GNDB), U3.20 (GNDB), U3.26 (GNDA), U3.27 (GNDA), U3.28 (GNDA); also elsewhere on the board
IN1: U1.9 (LED3), U2.3 (IN1)
IN2: U1.10 (LED4), U2.2 (IN2)
INA: R20.2, U1.6 (LED0)
INB: R21.2, U1.7 (LED1)
unnamed: D4.1 (KA), R30.1
unnamed: J6.1, U2.6 (OUT1)
unnamed: J6.2, U2.8 (OUT2)
unnamed: Q1.4 (G), U3.11 (CP)
unnamed: R11.2, U1.23 (~OE)
unnamed: R20.1, U3.4 (INA)
unnamed: R21.1, U3.10 (INB)
unnamed: R22.1, U3.7 (PWM)
unnamed: R23.1, R25.2, U3.5 (EN/DIAGA)
unnamed: R24.1, R27.2, U3.9 (EN/DIAGB)
unnamed: R26.1, R28.1, U3.8 (CS)
unnamed: R29.1, U2.4 (ILIM)
unnamed: TP1.1, U3.6 (CS_DIS)
OUTA: D4.2 (AK), J5.1, U3.1 (OUTA), U3.25 (OUTA), U3.30 (OUTA), U3.33 (OUTA); also elsewhere on the board
OUTB: J5.2, R30.2, U3.15 (OUTB), U3.16 (OUTB), U3.21 (OUTB), U3.32 (OUTB); also elsewhere on the board
SCL: R13.2, U1.26 (SCL); also elsewhere on the board
SDA: R12.2, U1.27 (SDA); also elsewhere on the board
STEERING_POS_ADC: J6.4; also elsewhere on the board
VBUS: C12.1, C13.1, C14.1, Q1.1 (S), Q1.2 (S), Q1.3 (S), U2.5 (VM), U3.12 (VBAT); also elsewhere on the board
VCC: C15.1, C16.1, Q1.5 (D), U3.3 (VCC), U3.13 (VCC), U3.23 (VCC), U3.31 (VCC)

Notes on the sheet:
DRIVE MOTOR
STEERING SERVO
PWM DRIVER - PCA9685PW I2C ADDRESS: 1000_000X (0x80) SHIFTED ADY: 0100_1000 (0x40)
FOR REV B: Flip pin mapping for J6 1 - GND 2 - RESDIV 3 - 5V 4 - OUT2 5 - OUT1

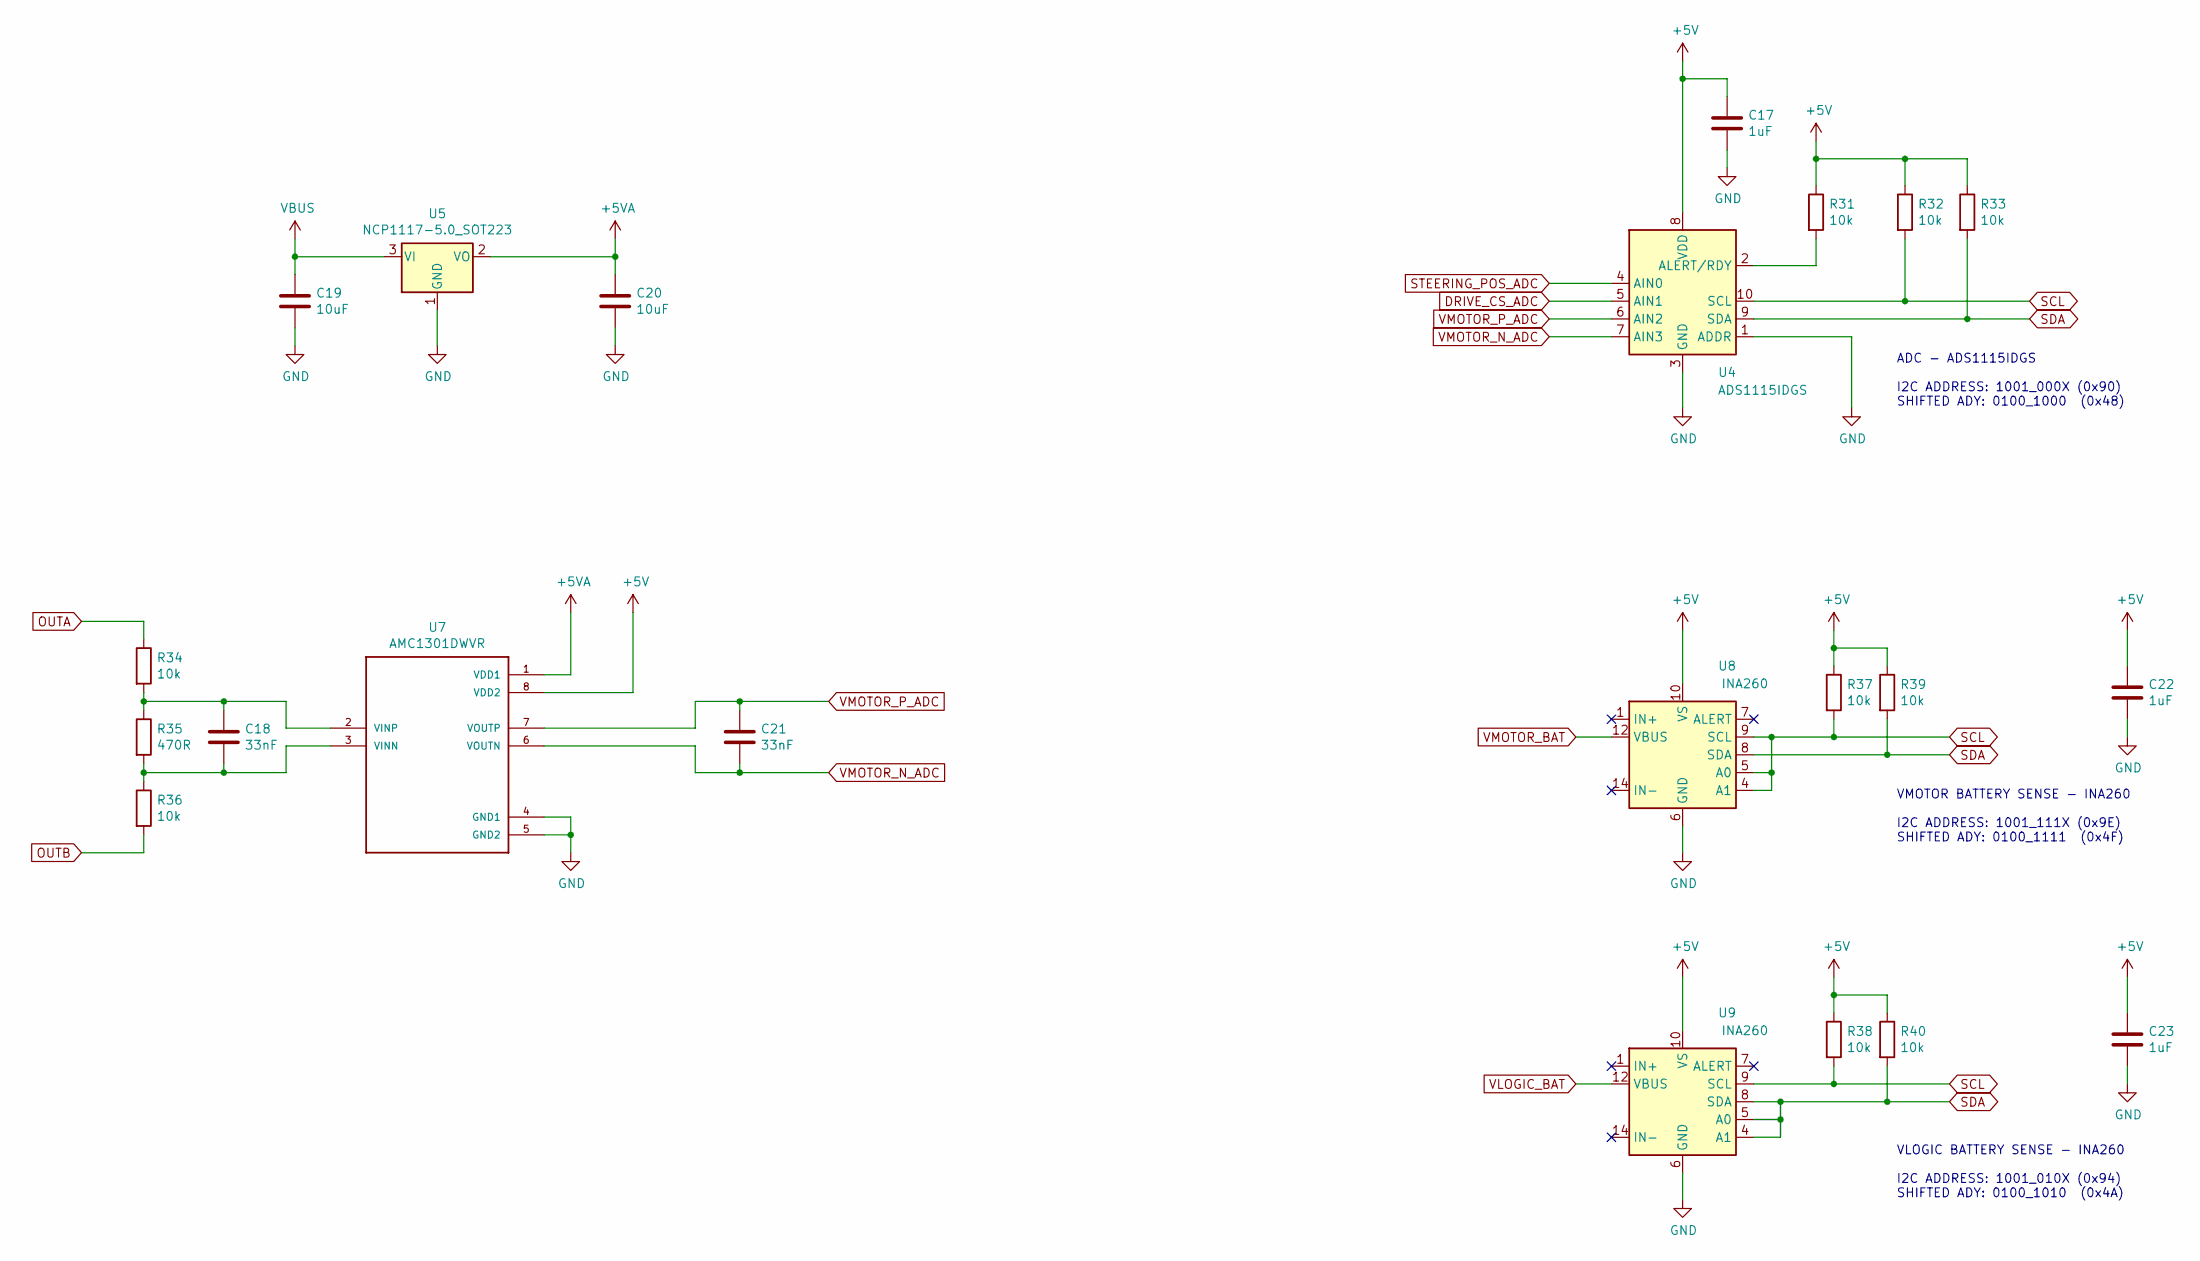
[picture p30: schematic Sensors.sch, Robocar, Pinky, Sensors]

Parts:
C17, C22, C23: 1uF; C_0805_2012Metric; MPN C0805C105K4RACTU
C18, C21: 33nF; C_0805_2012Metric; MPN C0805C333K5RACTU
C19, C20: 10uF; C_0805_2012Metric; MPN C0805C106K4PACTU
R31, R32, R33, R34, R36, R37, R38, R39, R40: 10k; R_0603_1608Metric; MPN RC0603FR-0710KL
R35: 470R; R_0603_1608Metric; MPN ESR03EZPJ471
U4: ADS1115IDGS; TSSOP-10_3x3mm_P0.5mm; MPN ADS1115IDGSR
U5: NCP1117-5.0_SOT223; SOT-223-3_TabPin2; MPN NCP1117LPST50T3G
U7: AMC1301DWVR; SOIC127P1150X280-8N; MPN AMC1301DWVR
U8, U9: INA260; TSSOP-16_4.4x5mm_P0.65mm; MPN INA260AIPW

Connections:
+5V: C17.1, C22.1, C23.1, R31.1, R32.1, R33.1, R37.1, R38.1, R39.1, R40.1, U4.8 (VDD), U7.8 (VDD2), U8.10 (VS), U9.10 (VS); also elsewhere on the board
+5VA: C20.1, U5.2 (VO), U7.1 (VDD1)
DRIVE_CS_ADC: U4.5 (AIN1); also elsewhere on the board
GND: C17.2, C19.2, C20.2, C22.2, C23.2, U4.1 (ADDR), U4.3 (GND), U5.1 (GND), U7.4 (GND1), U7.5 (GND2), U8.6 (GND), U8.11 (GND), U9.6 (GND), U9.11 (GND); also elsewhere on the board
unnamed: C18.1, R34.2, R35.1, U7.2 (VINP)
unnamed: C18.2, R35.2, R36.1, U7.3 (VINN)
unnamed: R31.2, U4.2 (ALERT/RDY)
unnamed: U8.1 (IN+), U8.2 (IN+), U8.3 (IN+)
unnamed: U8.14 (IN-), U8.15 (IN-), U8.16 (IN-)
unnamed: U9.1 (IN+), U9.2 (IN+), U9.3 (IN+)
unnamed: U9.14 (IN-), U9.15 (IN-), U9.16 (IN-)
OUTA: R34.1; also elsewhere on the board
OUTB: R36.2; also elsewhere on the board
SCL: R32.2, R37.2, R38.2, U4.10 (SCL), U8.4 (A1), U8.5 (A0), U8.9 (SCL), U9.9 (SCL); also elsewhere on the board
SDA: R33.2, R39.2, R40.2, U4.9 (SDA), U8.8 (SDA), U9.4 (A1), U9.5 (A0), U9.8 (SDA); also elsewhere on the board
STEERING_POS_ADC: U4.4 (AIN0); also elsewhere on the board
VBUS: C19.1, U5.3 (VI); also elsewhere on the board
VLOGIC_BAT: U9.12 (VBUS); also elsewhere on the board
VMOTOR_BAT: U8.12 (VBUS); also elsewhere on the board
VMOTOR_N_ADC: C21.2, U4.7 (AIN3), U7.6 (VOUTN)
VMOTOR_P_ADC: C21.1, U4.6 (AIN2), U7.7 (VOUTP)

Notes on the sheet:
ADC - ADS1115IDGS I2C ADDRESS: 1001_000X (0x90) SHIFTED ADY: 0100_1000 (0x48)
VMOTOR BATTERY SENSE - INA260 I2C ADDRESS: 1001_111X (0x9E) SHIFTED ADY: 0100_1111 (0x4F)
VLOGIC BATTERY SENSE - INA260 I2C ADDRESS: 1001_010X (0x94) SHIFTED ADY: 0100_1010 (0x4A)

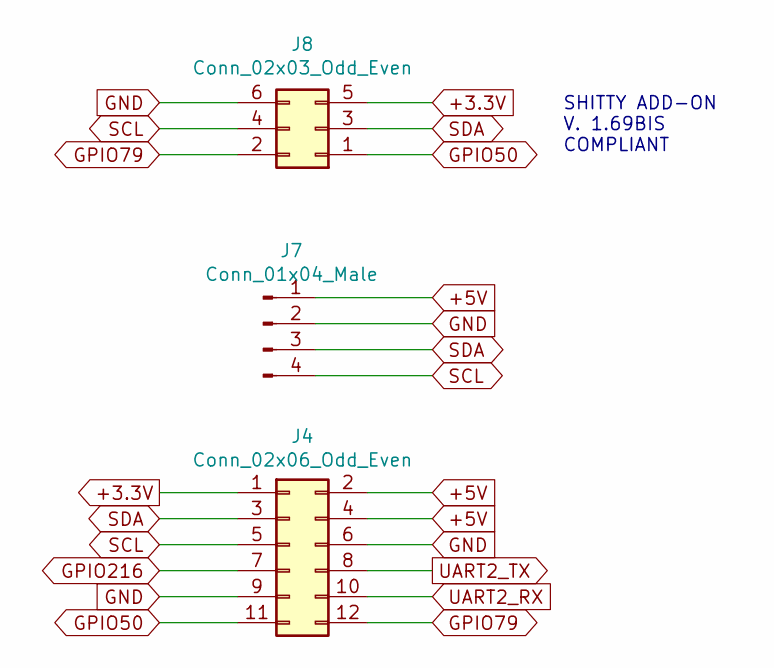
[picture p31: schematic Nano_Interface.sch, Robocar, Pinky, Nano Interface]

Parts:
J4: Conn_02x06_Odd_Even; PinHeader_2x06_P2.54mm_Vertical; MPN 67997-112HLF
J7: Conn_01x04_Male; PinHeader_1x04_P2.54mm_Vertical
J8: Conn_02x03_Odd_Even; IDC-Header_2x03_P2.54mm_Vertical; MPN SFH11-NBPC-D03-ST-BK

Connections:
+3.3V: J4.1, J8.5
+5V: J4.2, J4.4, J7.1; also elsewhere on the board
GND: J4.6, J4.9, J7.2, J8.6; also elsewhere on the board
GPIO50: J4.11, J8.1
GPIO79: J4.12, J8.2
GPIO216: J4.7
SCL: J4.5, J7.4, J8.4; also elsewhere on the board
SDA: J4.3, J7.3, J8.3; also elsewhere on the board
UART2_RX: J4.10
UART2_TX: J4.8

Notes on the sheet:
SHITTY ADD-ON V. 1.69BIS COMPLIANT

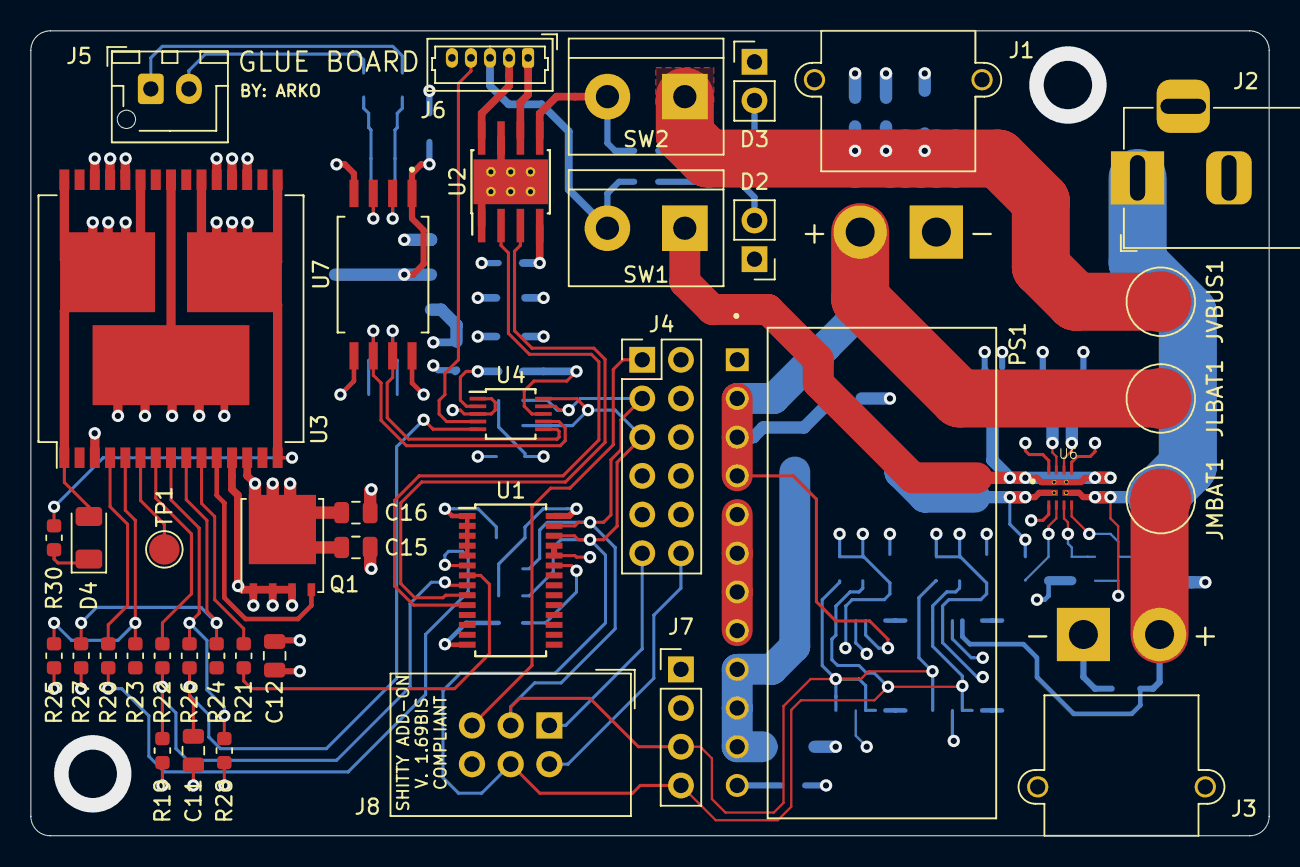
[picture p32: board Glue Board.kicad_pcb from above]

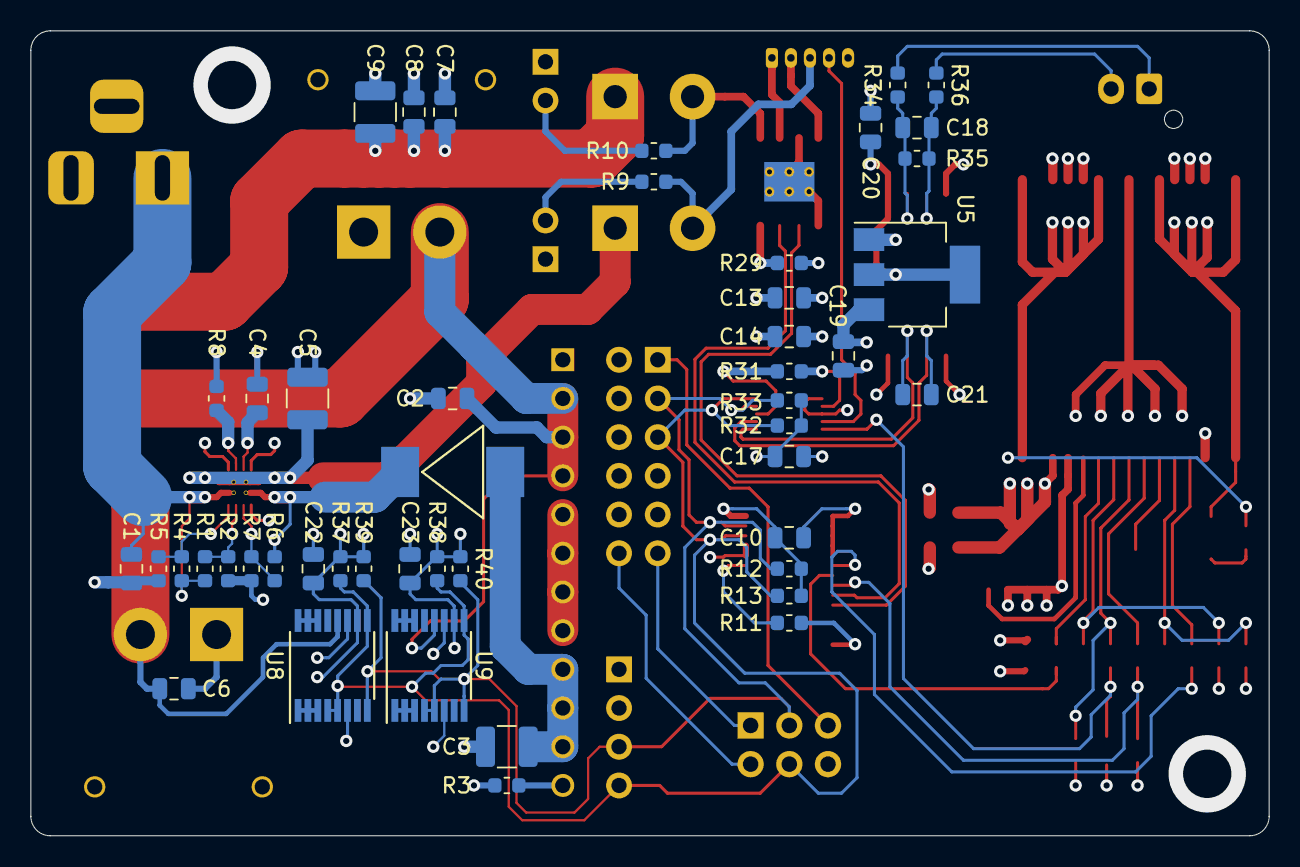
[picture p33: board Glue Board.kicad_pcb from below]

Board: 4 copper layers, 81.3 x 52.8 mm, 87 parts (47 on the bottom side), 56 nets.

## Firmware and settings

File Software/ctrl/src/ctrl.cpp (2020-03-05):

/**************************************************************************/
/*!
    @file     ctrl.cpp
    @author   Arko
    @license  BSD (see license.txt)
    Robocar Control Program
    v1.0 - First release
*/
/**************************************************************************/

#include <pthread.h>
#include <sched.h>
#include <signal.h>
#include <time.h>
#include <sys/time.h>
#include <sys/types.h>
#include <sys/ipc.h>
#include <sys/sem.h>
#include <sys/shm.h>
#include <stdio.h>
#include <stdlib.h>
#include <string.h>
#include <unistd.h>
#include <inttypes.h>
#include <errno.h>
#include <math.h>

#include "ctrl.h"
#include "comm.h"

extern "C" {
  #include "glue.h"
}

// Local Variables
bool volatile ctrl_run = true;                  // Control loop run state

int64_t ctrl_loop_period = CTRL_LOOP_PERIOD;	// 50ms -> 20Hz, value in nanoseconds
int64_t tosleep;                                // slack time, nanoseconds to sleep till next ctrl loop call 

uint32_t missed_heartbeat_count = 0;            // Count missed heartbeat, estop at max cnt
uint32_t last_heartbeat = 0;                    // Last heartbeat value, should increase monotonically

// Local Communication Variables
Ctrl_Cmd ctrl_cmd;                              // Command data from C&DH
Ctrl_Telem ctrl_telem;                          // Telemetry data to C&DH

// Steering Motor PID Variables
float steer_desired_pos = 0.0;
float steer_actual_pos = 0.0;
float steer_error_pos = 0.0;
float steer_error_pos_prior = 0.0;
float steer_i_accu = 0.0;
float steer_p = 0.0;
float steer_i = 0.0;
float steer_d = 0.0;
float steer_out = 0.0;

// Drive Motor PID Variables
float drive_desired_vel = 0.0;
float drive_actual_vel = 0.0;
float drive_error_vel = 0.0;
float drive_error_vel_prior = 0.0;
float drive_i_accu = 0.0;
float drive_p = 0.0;
float drive_i = 0.0;
float drive_d = 0.0;
float drive_f = 0.0;
float drive_out = 0.0;

/**************************************************************************/
/*!
    @brief  Control program main
    @param  argc    Arguement count
    @param  argv    Arguement variables
    @return Error code
*/
/**************************************************************************/
int main(int argc, char *argv[])
{
    // ========================================================================
    // Initalize system
    // ========================================================================
    printf("=== ROBOCAR - CTRL: START ===\n");

    // Make sure ctrl-C stops the program under controlled circumstances
    signal(SIGINT, &sigint);

    // Initalize Communication to C&DH
    printf("Initializing comm shared memory...\n");
    if(comm_init() == 0)
    {
	    printf("ERROR: Comm init failed.\n");
	    exit(1);
    }

    // Initialize Glue Board
    printf("Initalizing glue board...\n");
    glue_init();

    // Initialize the control state machine to ESTOP mode
    ctrl_telem.mode = ESTOP;
    // ========================================================================

    // ========================================================================
    // Configure and start real-time thread
    // ========================================================================
    // Create attributes for an isolated real-time thread
    printf("Starting isolated soft real-time control loop thread...\n");
    pthread_attr_t attr = {};
    pthread_attr_init(&attr);
    // Lift the thread off core 3, which takes system interrupts
    cpu_set_t cpuset = {};
    CPU_ZERO(&cpuset);
    CPU_SET(3, &cpuset);
    pthread_attr_setaffinity_np(&attr, 1, &cpuset);
    // Make it use FIFO policy for "soft" real-time scheduling
    pthread_attr_setschedpolicy(&attr, SCHED_FIFO);
    pthread_attr_setinheritsched(&attr, PTHREAD_EXPLICIT_SCHED);
    // Set the priority
    sched_param param = {};
    param.sched_priority = 1;
    pthread_attr_setschedparam(&attr, &param);

    // Create the real-time thread
    pthread_t ctrl_thread;
    int err;
    if ((err = pthread_create(&ctrl_thread, &attr, &ctrl_timer_func, NULL)) != 0) {
        char const *emsg = ((err == EAGAIN) ? "EAGAIN" : ((err == EINVAL) ? "EINVAL" : ((err == EPERM) ? "EPERM" : "unknown")));
        fprintf(stderr, "pthread_create() failed (%d %s); are you sure you're root?\n", err, emsg);
        fprintf(stderr, "You may also need to do:\n");
        fprintf(stderr, "echo -1 > /proc/sys/kernel/sched_rt_runtime_us\n");
        exit(1);
    }

    // Wait for the program to be done
    void *ignore = NULL;
    pthread_join(ctrl_thread, &ignore);
    // ========================================================================

    // ========================================================================
    // Shutdown system
    // ========================================================================
    // Real time thread exited
    printf("Real-time thread exited.\n");

    // Stop all motors
    glue_estop();
    printf("ESTOP!\n");

    // Close communication shared memory
    comm_close();
    printf("Comm shared memory closed.\n");

    printf("=== ROBOCAR - CTRL: STOP ===\n");
    // ========================================================================

    return 0;
}

/**************************************************************************/
/*!
    @brief  Control timer function calls the control loop function at
            a specified frequency.
    @return Error code
*/
/**************************************************************************/
void *ctrl_timer_func(void *) {

    //  keep track of the passage of time at a 20-millisecond quantized interval
    struct timespec last = {}, now = {};
    clock_gettime(CLOCK_MONOTONIC_RAW, &last);

    while (ctrl_run) 
    {
        clock_gettime(CLOCK_MONOTONIC_RAW, &now);
        //  20 milliseconds, as nanoseconds
        tosleep = ctrl_loop_period - (now.tv_sec - last.tv_sec) * 1000000000 - (now.tv_nsec - last.tv_nsec);

        if(tosleep < 0)
        {
            printf("ERROR: SCHEDULED CONTROL LOOP ROUTINE OVERRAN!!! - TOSLEEP = %" PRId64 "\n", tosleep);
            printf("RESETTING CLOCK...");
            last = now;
            tosleep = 0;
        }
        else
        {
            printf("TOSLEEP = %" PRId64 ", ", tosleep);
        }

        last.tv_nsec += ctrl_loop_period;
        if (last.tv_nsec >= 1000000000) {
            last.tv_nsec -= 1000000000;
            last.tv_sec += 1;
        }
        if (tosleep > (2*ctrl_loop_period)) {
            //  missed by more than one full interval! re-set the clock basis
            last = now;
            tosleep = 0;
        }
        if (tosleep > 0) {
            struct timespec slp = {};
            slp.tv_nsec = (long)tosleep;
            nanosleep(&slp, NULL);
        }

        // ========================================================================
        // Control System Main Loop
        // ========================================================================
        ctrl_loop();
        // ========================================================================
    }

    return NULL;
}

/**************************************************************************/
/*!
    @brief  Control loop function implements a state machine driven by an
            external program to read the sensors and drive actuators.
            Fault protection cuts motor power when communication with the
            external program is lost.
    @return Error code
*/
/**************************************************************************/
int ctrl_loop(void)
{
    // ========================================================================
    // Update telemetry
    // ========================================================================
    // Update ToSleep for debug telemetry
    ctrl_telem.tosleep = tosleep;

    // Incremement timestamp
    ctrl_telem.timestamp += 1;

    // Read and print state
    ctrl_telem.glue_state = glue_state_update();

    // If in debug mode, print raw telem
    #ifdef TELEM_DEBUG
        printf("TIME = %i,", ctrl_telem.timestamp);
        glue_print(ctrl_telem.glue_state);
        printf("CMDSTRPOS = %f, CMDDRVVEL = %f\n", ctrl_cmd.steer_pos, ctrl_cmd.drive_vel);
    #endif
    // ========================================================================

    // ========================================================================
    // Control state machine
    // ========================================================================
    switch (ctrl_telem.mode)
    {
        case ESTOP:                             // Emergency Stop - Zero actuators
            printf("MODE: EMERGENCY STOP\n");
            glue_estop();
            break;

        case INIT:                              // Initialize drive parameters
            printf("MODE: INIT\n");
            // Zero steering and drive motor PID variables
            steer_desired_pos = 0.0;
            steer_actual_pos = 0.0;
            steer_error_pos = 0.0;
            steer_error_pos_prior = 0.0;
            steer_i_accu = 0.0;
            steer_p = 0.0;
            steer_i = 0.0;
            steer_d = 0.0;
            steer_out = 0.0;
            drive_desired_vel = 0.0;
            drive_actual_vel = 0.0;
            drive_error_vel = 0.0;
            drive_error_vel_prior = 0.0;
            drive_i_accu = 0.0;
            drive_p = 0.0;
            drive_i = 0.0;
            drive_d = 0.0;
            drive_f = 0.0;
            drive_out = 0.0;
            // Set motor values
            glue_set_steering_motor(steer_out);
            glue_set_drive_motor(drive_out);
            break;

        case IDLE:                              // Idle waiting for race to start
            printf("MODE: IDLE\n");
            break;

        case RUN:                               // Run the race
            printf("MODE: RUN\n");
            // ================================================================
            // Steering Position PID Controller
            // ================================================================
            // Convert steering encoder voltage to normalized steering position value
            steer_actual_pos = STEER_SCALER * (STEER_ZERO_VAL - ctrl_telem.glue_state.steer_position);

            // Set commanded steering position as the new goal position
            steer_desired_pos = ctrl_cmd.steer_pos;

            // Calculate steering position error
            steer_error_pos = steer_desired_pos - steer_actual_pos;

            // Update integral accumulator
            steer_i_accu = steer_i_accu + (steer_error_pos * DT);

            // Steering PID terms
            steer_p = STEER_P_GAIN * steer_error_pos;
            steer_i = STEER_I_GAIN * steer_i_accu;
            steer_d = STEER_D_GAIN * (steer_error_pos - steer_error_pos_prior);

            // Sanitize integral term
            if(steer_i > STEER_I_LIMIT)
            {
                steer_i = STEER_I_LIMIT;
            }
            if(steer_i < -1.0*STEER_I_LIMIT)
            {
                steer_i = -1.0*STEER_I_LIMIT;
            }

            // Caluclate PID output
            steer_out = steer_p + steer_i + steer_d;

            // Store position error for next D term calculation
            steer_error_pos_prior = steer_error_pos;

            // Sanitize the steering motor output value
            if(steer_out > STEER_OUT_LIMIT)
            {
                steer_out = STEER_OUT_LIMIT;
            }
            if(steer_out < -1.0 * STEER_OUT_LIMIT)
            {
                steer_out = -1.0 * STEER_OUT_LIMIT;
            }
            // ================================================================

            // ================================================================
            // Drive Velocity PIDF Controller
            // ================================================================
            // Convert drive motor voltage to normalize drive velocity value
            drive_actual_vel = DRIVE_SCALER * (DRIVE_ZERO_VAL - ctrl_telem.glue_state.drive_velocity);

            // Set commanded drive velocity as the new goal velocity
            drive_desired_vel = ctrl_cmd.drive_vel;

            // Calculate drive velocity error
            if(drive_desired_vel > 0.01 || drive_desired_vel < -0.01)
            {
                drive_error_vel = drive_desired_vel - drive_actual_vel;
            }
            else
            {
                drive_error_vel = 0.0;
            }

            // Update integral accumulator
            drive_i_accu = drive_i_accu + (drive_error_vel * DT);

            // Drive PIDF terms
            drive_p = DRIVE_P_GAIN * drive_error_vel;
            drive_i = DRIVE_I_GAIN * drive_i_accu;
            drive_d = DRIVE_D_GAIN * (drive_error_vel - drive_error_vel_prior);
            drive_f = DRIVE_F_GAIN * drive_desired_vel;

            // Sanitize integral accumulator
            if(drive_i > DRIVE_I_LIMIT)
            {
                drive_i = DRIVE_I_LIMIT;
            }
            if(drive_i < -1.0*DRIVE_I_LIMIT)
            {
                drive_i = -1.0*DRIVE_I_LIMIT;
            }

            // Calculate PIDF output
            drive_out = drive_p + drive_i + drive_d + drive_f;

            // Store velocity error for next D term calculation
            drive_error_vel_prior = drive_error_vel;

            // Sanitize the drive motor output value
            if(drive_out > DRIVE_OUT_LIMIT)
            {
                drive_out = DRIVE_OUT_LIMIT;
            }
            if(drive_out < -1.0 * DRIVE_OUT_LIMIT)
            {
                drive_out = -1.0 * DRIVE_OUT_LIMIT;
            }
            // ================================================================

            // ================================================================
            // Set steering and drive motor outputs
            // ================================================================
            glue_set_steering_motor(steer_out);
            glue_set_drive_motor(drive_out);
            // ================================================================

            #ifdef PID_TUNING_DEBUG
                ctrl_print_pid();
            #endif
            break;

        case STOP:                              // Stop racing
            printf("MODE: STOP\n");
            glue_set_drive_motor(0);
            glue_set_steering_motor(0);
            break;

        case FAULT:                             // Error occured, ESTOP and phone home
            printf("MODE: FAULT\n");
            glue_estop();
            break;

        case CLEARFAULT:                        // Clear the error, and go to ESTOP state
            printf("MODE: CLEAR FAULT");
	        missed_heartbeat_count = 0;
            ctrl_telem.mode = ESTOP;
            break;

        default:                                // If all else fails, ESTOP and phone home
            printf("MODE: FATAL\n");
            glue_estop();
            break;
    }
    // ========================================================================

    // ========================================================================
    // Copy the latest telemetry/command data from shared memory to local memory
    // ========================================================================
    comm_transaction(&ctrl_cmd, &ctrl_telem);
    // ========================================================================

    // ========================================================================
    // Fault protection and mode command handler
    // ========================================================================
    if(ctrl_telem.mode != FAULT)    // No faults, continue
    {
        // Timeout based deadman switch
        // If we lose too many heartbeat counts, issue an ESTOP
        // Else accept the new command mode
        if(last_heartbeat < ctrl_cmd.heartbeat)
        {
            // Store the new heartbeat count value
            last_heartbeat = ctrl_cmd.heartbeat;

            // Reset missed heartbeat counter
            missed_heartbeat_count = 0;

            // Set the control mode for the next cycle based on what is commanded
            ctrl_telem.mode = ctrl_cmd.mode;
        }
        else
        {
            if(missed_heartbeat_count >= MAX_MISSED_HEARTBEAT)
            {
                ctrl_telem.mode = FAULT;
            }
            else
            {
                missed_heartbeat_count++;
            }
        }
    }
    else                            // Fault state, wait for clear fault command
    {
        if(ctrl_cmd.mode == CLEARFAULT)
        {
            ctrl_telem.mode = ctrl_cmd.mode;
        }
    }
    // ========================================================================

    return 1;
}

/**************************************************************************/
/*!
    @brief  Signal interrupt to kill real-time control thread
*/
/**************************************************************************/
void sigint(int) 
{
    ctrl_run = false;
}

/**************************************************************************/
/*!
    @brief  Print PID data for debug
    @return None
*/
/**************************************************************************/
void ctrl_print_pid(void)
{
    printf("STR_ERR = %.5f, STR_OUT = %.5f, STR_P = %.5f, STR_I = %.5f, STR_D = %.5f, ",\
        steer_error_pos, \
        steer_out, \
        steer_p, \
        steer_i, \
        steer_d);

    printf("DRV_DES = %.5f, DRV_ACT = %.5f, DRV_ERR = %.5f, DRV_OUT = %.5f, DRV_P = %.5f, DRV_I = %.5f, DRV_D = %.5f, DRV_F = %.5f\r\n",\
        drive_desired_vel, \
        drive_actual_vel, \
        drive_error_vel, \
        drive_out, \
        drive_p, \
        drive_i, \
        drive_d, \
        drive_f);
}

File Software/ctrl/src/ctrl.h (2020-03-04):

#ifndef __CTRL_H__
#define __CTRL_H__

// Control Configuration Parameters
#define TELEM_DEBUG             1
//#define PID_TUNING_DEBUG        1
#define CTRL_LOOP_PERIOD        50000000                   // dt in nanoseconds
#define MAX_MISSED_HEARTBEAT    25                         // Fault if exceeded

#define DT                      (CTRL_LOOP_PERIOD/1000000) // dt in milliseconds

#define STEER_P_GAIN        1.000
#define STEER_I_GAIN        0.0005
#define STEER_D_GAIN        0.000
#define STEER_I_LIMIT       0.200
#define STEER_OUT_LIMIT     0.800
#define STEER_LEFT_MAX_VAL  3.000
#define STEER_ZERO_VAL      2.400
#define STEER_RIGHT_MAX_VAL 1.800
#define STEER_SCALER        (STEER_RIGHT_MAX_VAL - STEER_LEFT_MAX_VAL)/2

#define DRIVE_P_GAIN        0.000
#define DRIVE_I_GAIN        0.000
#define DRIVE_D_GAIN        0.000
#define DRIVE_F_GAIN        0.500
#define DRIVE_I_LIMIT       0.000
#define DRIVE_OUT_LIMIT     0.100
#define DRIVE_REV_MAX_VAL   2.600
#define DRIVE_ZERO_VAL      1.400
#define DRIVE_FWD_MAX_VAL   0.300
#define DRIVE_SCALER        (DRIVE_REV_MAX_VAL - DRIVE_FWD_MAX_VAL)/2

extern "C" {
    #include "glue.h"
}

void *ctrl_timer_func(void *);
void sigint(int);
int ctrl_loop(void);
void ctrl_print_pid(void);

#endif // __CTRL_H__

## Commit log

2019-12-26 Updated with block diagram and bill of materials
    Updated with block diagram and bill of materials
2019-12-27 Started "Glue Board" PCB
    Started "Glue Board" PCB
    [Actuators.sch, Glue Board.kicad_pcb, Glue Board.sch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]
2019-12-28 Finished the schematic for the most parts
    Finished the schematic for the most parts
    [Actuators.sch, Glue Board.kicad_pcb, Glue Board.sch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]
2019-12-29 Complete Schematic and BOM
    Complete Schematic and BOM. Next up, layout!
    [Actuators.sch, Glue Board.csv, Glue Board.kicad_pcb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]
2019-12-30 Added Motor v-sense and battery mon. Layout time!
    Added Motor v-sense and battery mon. Layout time!
    [Actuators.sch, Glue Board.csv, Glue Board.kicad_pcb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]
2019-12-31 Glue Board - Rev A - Production
    Glue Board - Rev A - Production
    [Glue Board-B_Cu.gbr, Glue Board-B_Mask.gbr, Glue Board-B_Paste.gbr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]
2020-01-02 added oCamS Software
    [cam.cfg]
2020-01-05 Abandoning the oCamS stereo cam and switching to ZED Mini due to support issues with Ubuntu 18 and ROS Melodic.
    [cam.cfg]
2020-01-22 Abandoned oCamS for ZED Mini and updated Glue Board
    Abandoned oCamS for ZED Mini and updated Glue Board
    [Base Plate v27.stl, Battery Bottom Plate v7.stl, Battery Side Wall v5.stl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]
2020-01-25 Updated Readme
    Updated Readme
    [Actuators.sch, Sensors.sch]
2020-01-27 Added harnessing and assembly diagrams
    Added harnessing and assembly diagrams
    [Actuators.sch, Glue Board.kicad_pcb, Glue_Board_BOM.xlsx]
2020-01-27 Started rc_ctrl. Working i2c example build
2020-01-27 more repairs
    [ZED.stl, ZEDM.stl, Zed.cfg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]
2020-01-29 Added raw open source libraries for the i2c devices
    Added raw open source libraries for the i2c devices. Next step is to modify them to work with the i2c libraries.
2020-02-01 Working voltage measurement using INA260 via I2C
2020-02-03 Initial attempt at porting all the i2c device libraries
    Initial attempt at porting all the i2c device libraries
2020-02-03 All i2c device libraries build and have undergone minimal testing. Next up... real testing
2020-02-05 Fixed 8bit/16bit read/write error. Next step is to propagate these changes to other functions within the project
    [ina260.c]
2020-02-05 Patched the 8/16bit word issue with I2C R/W
    Patched the 8/16bit word issue with I2C R/W
    [ads1115.c, ina260.c, pca9685.c]
2020-02-05 Working PWM. ADS1115 still giving bogus values.
2020-02-06 Working ADC1115! It was mostly a schematic error.
    [ads1115.c]
2020-02-06 Added schematic change notes for REV B
    Added schematic change notes for REV B
    [Sensors.sch]
2020-02-06 Added robocar stand
    Added robocar stand
    [Stand v2.stl]
2020-02-09 Moved glue board test code into glue.c
    Moved glue board test code into glue.c. More coding/testing required.
2020-02-11 Functional wheel spin code!
2020-02-11 Modified I2C to run faster by increasing the clock speed and decreasing the delay time between r/w
2020-02-11 Updated readme to reflect changes to jetson i2c config
    Updated readme to reflect changes to jetson i2c config
2020-02-11 Updated i2c to use 100us delays
    Updated i2c to use 100us delays
2020-02-12 First attempt at making a monotonic soft timer based control loop
    First attempt at making a monotonic soft timer based control loop
2020-02-14 Fixed C/C++ makefile errors
    [ctrl.cpp, ctrl.h]
2020-02-14 Working 50Hz control codegit add -A!
2020-02-16 Clean up complete. Next up? python decode/write/print, then PID controller
2020-02-17 Working C++/Python command/telem. Next is PID, then python overhaul to interface with user/prcp
2020-02-17 Fixed tabs/spacing to 4 spaces
    Fixed tabs/spacing to 4 spaces. Not sure why it took me so long to fix this...
    [ads1115.c, ctrl.cpp, ctrl.h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]
2020-02-18 Added PID+F controllers and some input sanitization
    Added PID+F controllers and some input sanitization
2020-02-19 Added PID tuning functions and cleaned up a bit
    Added PID tuning functions and cleaned up a bit
2020-02-19 Tuned steering PID gains. May require some tweaking when driving
2020-02-19 Best steering PID gains we will get prior to track testing. Next up, calibrate drive velocity measurements and tune gains
2020-02-19 Added wire cover stl
    Added wire cover stl
    [Wire cover v6.stl]
2020-02-20 Velocity gains are quote unquote good enough
2020-02-21 Started perception development, ran a basic image capture test only to learn that it slows down the soft real-time control software... problems to debug
    [ZED.stl, ZEDM.stl, Zed.cfg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]
2020-02-22 Due to resource constraints the control loop freq was brought down from 50Hz to 20Hz to allow the perception system to run with interfereing with the controller. This commit contains the good-enough 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
    [ctrl.cpp, ctrl.h]
2020-02-23 Added delay to reading the ADS1115. Previous channel values were bleeding over, so this delay fixed that. Without it, the drive velocity PID+F control goes unstable.
    [ctrl.h, glue.c]
2020-02-24 First track run at ROM! It works!
2020-02-26 Office track, EOD commit. Works fairly well, but I need a bigger track with less... yellow
2020-02-27 Doing laps in the living room but the velocity is laggy and oscillating. I think the vision system is far too slow and as a result, the steering lags significally... and it's jerky
    [ctrl.h]
2020-02-28 Smooth running ctrl (20Hz) and prcp (>20hz). No lane following yet, that's next
2020-03-03 Commit for the night.. need to fix the slow imshow functio
    [ctrl.h]
2020-03-04 Added granular lane detection and color coding, lane following based on camera velocity
2020-03-05 Fixed bugs
    Fixed bugs
    [prcp.hpp]
